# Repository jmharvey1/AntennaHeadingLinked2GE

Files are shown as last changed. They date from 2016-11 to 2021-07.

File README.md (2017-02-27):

# AntennaHeadingLinked2GE
These are the files used to link a common Antenna Rotor to Google Earth
For an overview of this project, please see YouTube Video found at:
https://youtu.be/OL32_ex3kCU

There is now a second set of files (Arduino sketch, and eagle circuit diagram) that supports
interfacing with an 8 wire CDE HAM III rotator control. 
The Python and Google Earth KLM files are the same for either interface

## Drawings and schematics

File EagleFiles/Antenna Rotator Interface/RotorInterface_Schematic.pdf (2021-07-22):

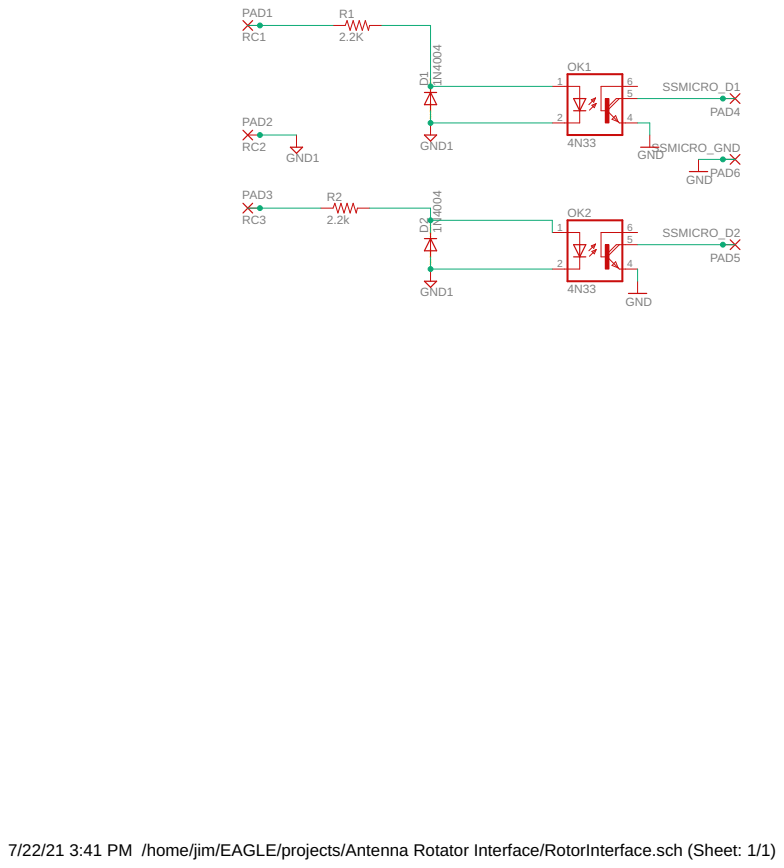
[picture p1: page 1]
GND; GND1; SSMICRO_D1; SSMICRO_D2; SSMICRO_GND; PAD1; PAD2; PAD3; PAD4; PAD5; PAD6

7/22/21 3:41 PM /home/jim/EAGLE/projects/Antenna Rotator Interface/RotorInterface.sch (Sheet: 1/1) SpiceOrder 1 SpiceOrder 2 SpiceOrder 1 SpiceOrder 2

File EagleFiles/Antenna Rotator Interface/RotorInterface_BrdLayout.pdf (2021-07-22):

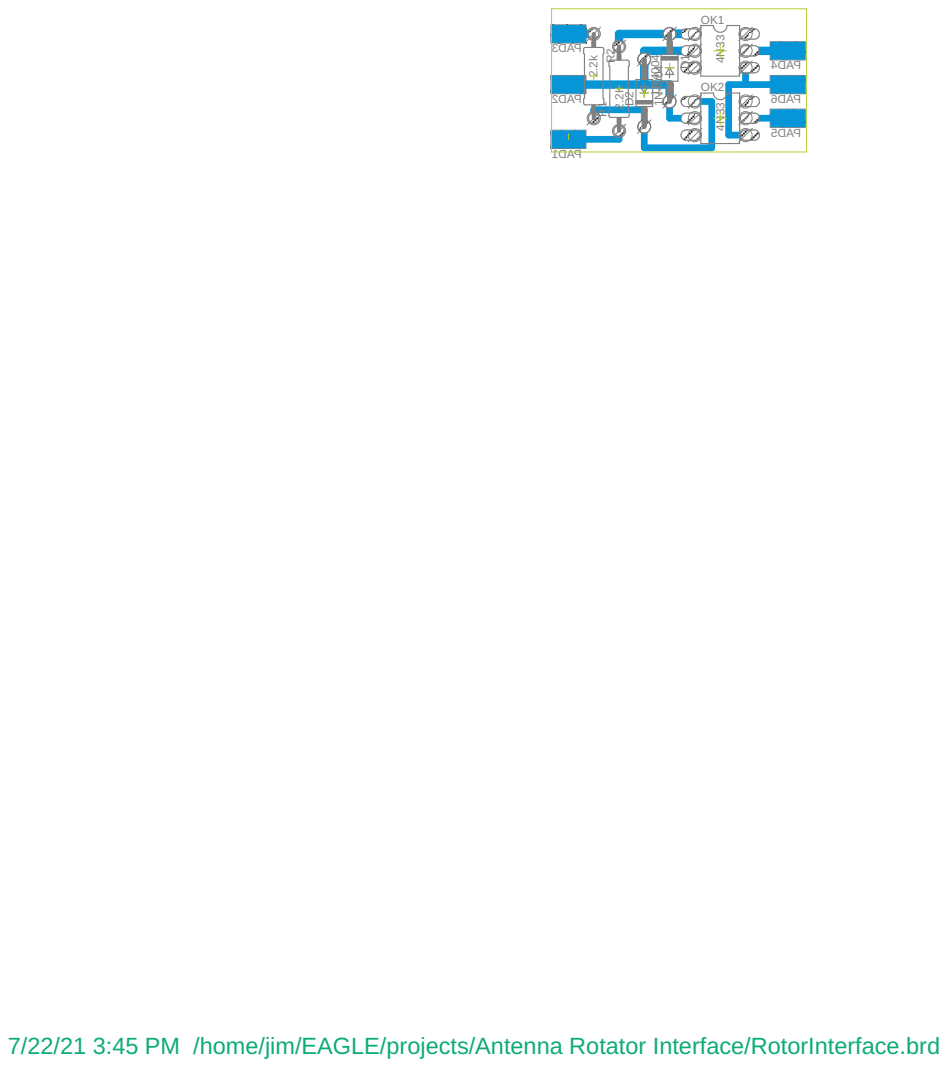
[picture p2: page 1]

7/22/21 3:45 PM /home/jim/EAGLE/projects/Antenna Rotator Interface/RotorInterface.brd

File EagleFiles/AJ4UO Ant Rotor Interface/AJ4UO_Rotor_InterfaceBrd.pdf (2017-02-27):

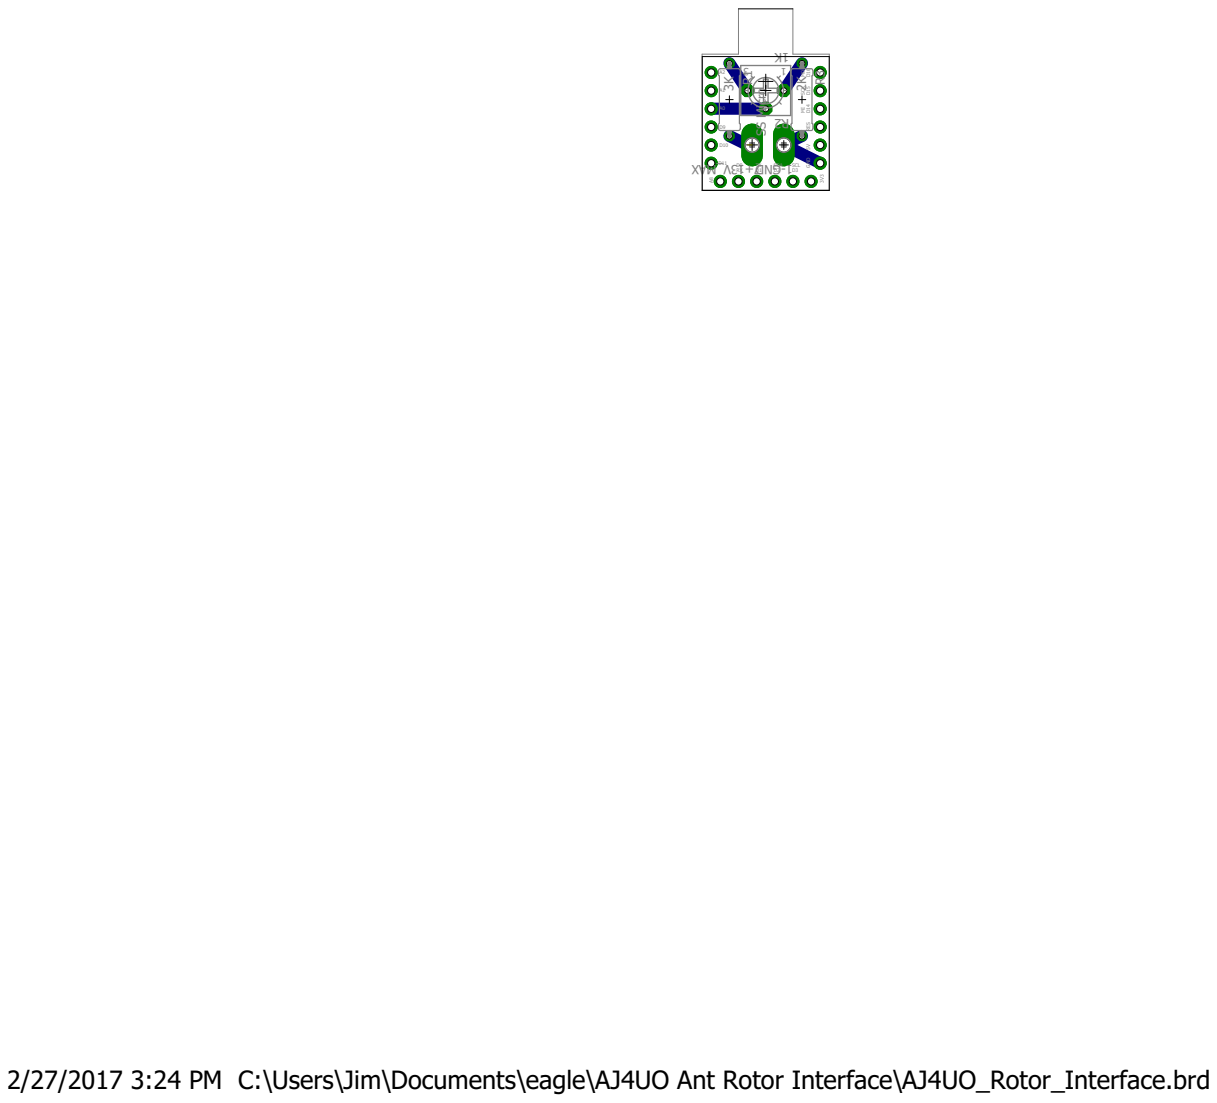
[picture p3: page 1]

2/27/2017 3:24 PM C:\Users\Jim\Documents\eagle\AJ4UO Ant Rotor Interface\AJ4UO_Rotor_Interface.brd

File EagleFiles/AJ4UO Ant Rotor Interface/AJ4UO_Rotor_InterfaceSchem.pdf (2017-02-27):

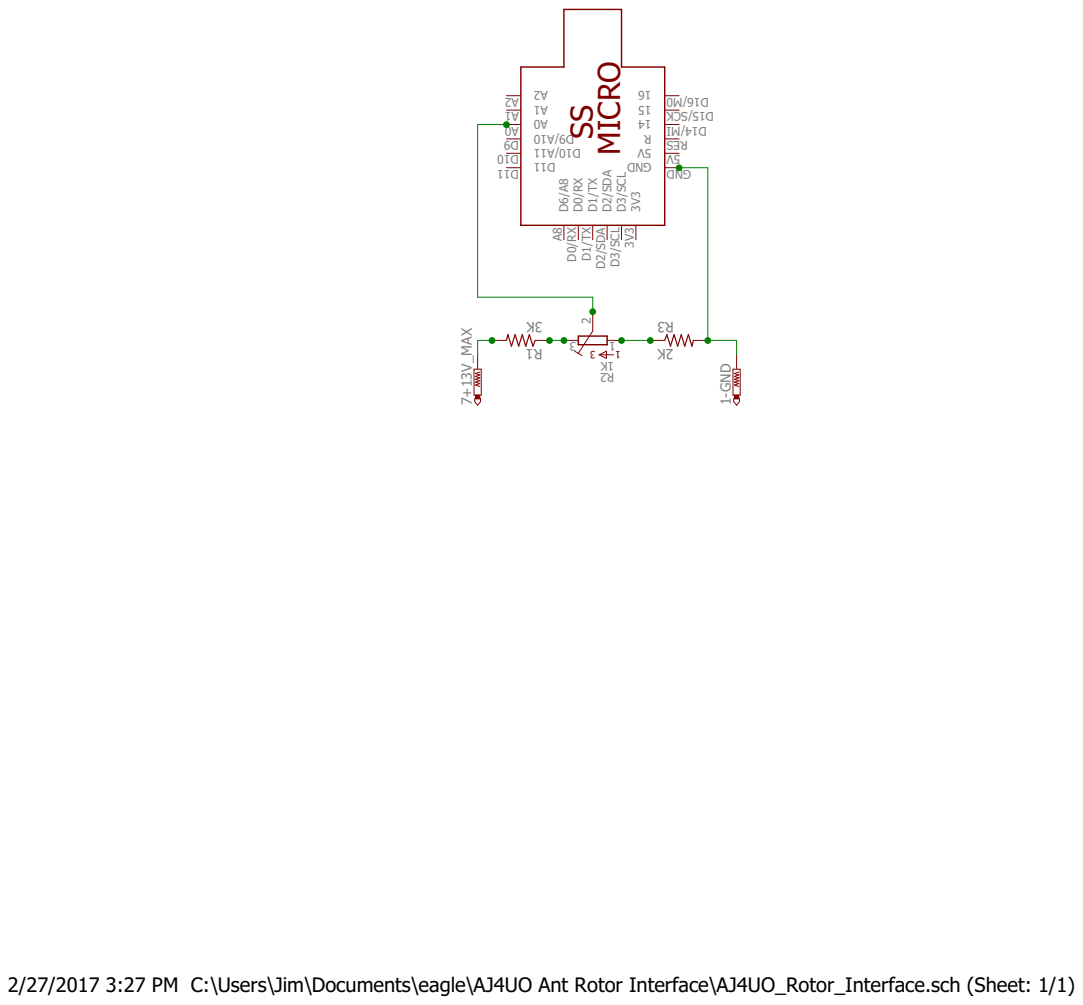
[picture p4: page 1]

D1/TX D1/TX D0/RX D0/RX D2/SDA D2/SDA D3/SCL D3/SCL

2/27/2017 3:27 PM C:\Users\Jim\Documents\eagle\AJ4UO Ant Rotor Interface\AJ4UO_Rotor_Interface.sch (Sheet: 1/1)

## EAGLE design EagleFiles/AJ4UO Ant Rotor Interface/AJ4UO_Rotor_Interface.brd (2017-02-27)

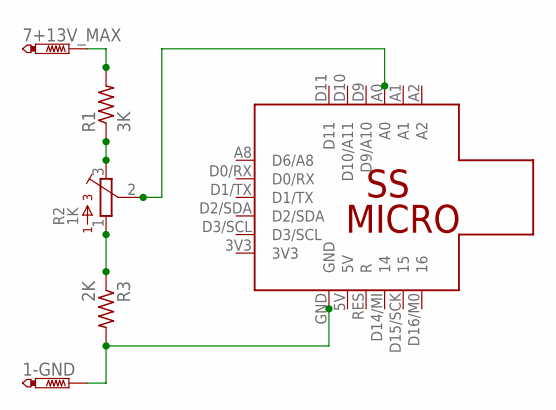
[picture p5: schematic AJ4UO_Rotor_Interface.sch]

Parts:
1-GND: 1 - GND; P1-20Y
7+13V_MAX: PTR1PAD1-20Y; P1-20Y
R1: 3K; 0309/10
R2: 1K; 3362P
R3: 2K; 0309/10
U$1: SS_MICRO

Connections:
unnamed: 1-GND.TP, R3.2, U$1.GND
unnamed: R2.1, R3.1
unnamed: R1.1, R2.3
unnamed: 7+13V_MAX.TP, R1.2
unnamed: R2.2, U$1.A0

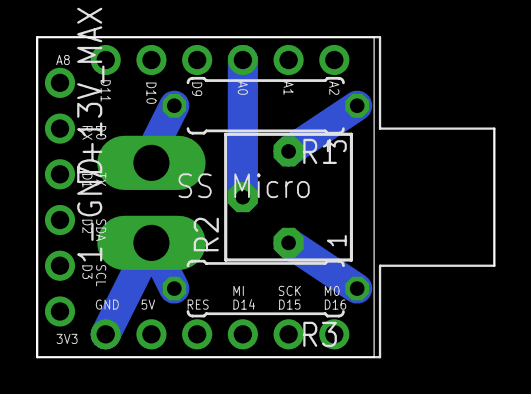
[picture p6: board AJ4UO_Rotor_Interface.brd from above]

Board: 2 copper layers, 18.7 x 17.8 mm, 6 parts (0 on the bottom side), 5 nets.

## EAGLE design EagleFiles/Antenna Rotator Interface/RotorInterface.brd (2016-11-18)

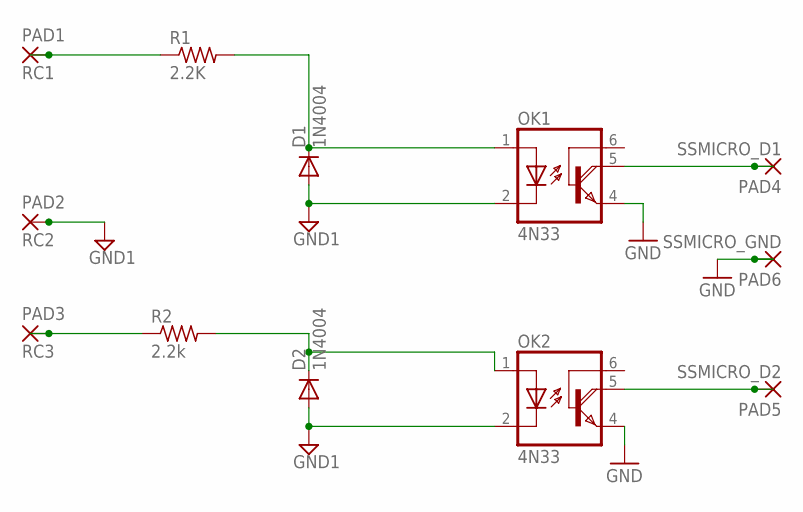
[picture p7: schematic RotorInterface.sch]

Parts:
D1, D2: 1N4004; DO41-10
OK1, OK2: 4N33; DIL06
PAD1: RC1; SMD2,54-5,08
PAD2: RC2; SMD2,54-5,08
PAD3: RC3; SMD2,54-5,08
PAD4: SSMICRO_D1; SMD2,54-5,08
PAD5: SSMICRO_D2; SMD2,54-5,08
PAD6: SSMICRO_GND; SMD2,54-5,08
R1: 2.2K; 0309/12
R2: 2.2k; 0309/12

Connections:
GND: OK1.4 (E), OK2.4 (E), PAD6.1
GND1: D1.A, D2.A, OK1.2 (C), OK2.2 (C), PAD2.1
unnamed: PAD3.1, R2.1
unnamed: PAD1.1, R1.1
unnamed: D1.C, OK1.1 (A), R1.2
unnamed: OK1.5 (COL), PAD4.1
unnamed: OK2.5 (COL), PAD5.1
unnamed: D2.C, OK2.1 (A), R2.2

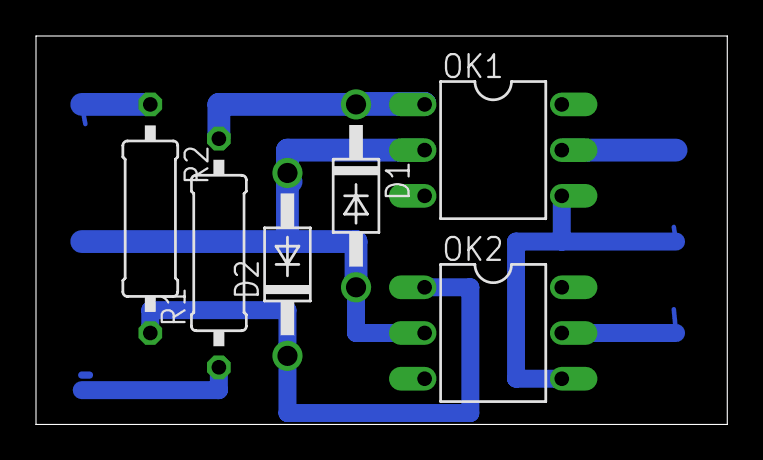
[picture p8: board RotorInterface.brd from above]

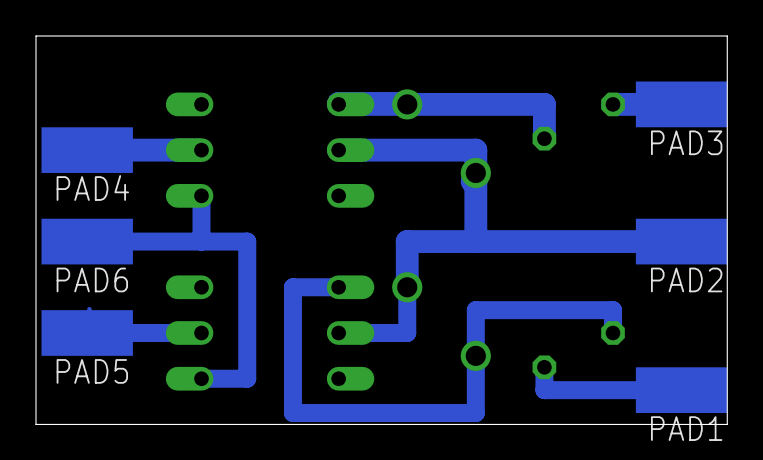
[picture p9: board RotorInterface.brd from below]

Board: 2 copper layers, 38.4 x 21.6 mm, 12 parts (6 on the bottom side), 8 nets.

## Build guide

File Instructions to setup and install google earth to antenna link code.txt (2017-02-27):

Note: The following instructions assume that "Google Earth" has been installed and is working
      on your computer. If not, download it here:
       https://earth.google.com/download-earth.html

1. To get copies of the Google Earth KML file, and the Python Script, needed for this project
   go to this Github site: 
             https://github.com/jmharvey1/AntennaHeadingLinked2GE
   Note: a recent version of the python script is also shown close to the the bottom of this file

2. To Download & Install the WAMPS server App, go to this Sourceforge location:
           https://sourceforge.net/projects/wampserver/?source=top3_dlp_t5
     or
           http://www.wampserver.com/
   
     from either of these two locations, you should be able to download the following file
          "wampserver3.0.6_x64_apache2.4.23_mysql5.7.14_php5.6.25-7.0.10.exe"      
     or the latest equivalent.
2a. Launch the execuexecutable/installer ("wampserver3.0.6_x64....  .exe") and follow the instructions

   Note: There is a Python/WAMP Server "install & setup" video found at:
               https://www.youtube.com/watch?v=bHyiXDJVjY8
   It shows the general process for installing the WAMP server and Python Applications.

3. Once installed, Start the WAMP server process (by clicking on the Desktop App ICON)
   
3a. As shown at 2:13 in the video mentioned above,
    What your are doing is modifing, the default "httpd.conf" file,
    to support Python file calls.
    To access it ("httpd.conf"), after launching the WAMP server process,
    left click the WAMP icon, in the lower tray.
    HighLight the "Apache" folder,
    And then select "httpd.conf", in the pick list that appears.

3b. Once you open the file, use notepad's "edit>find" menu option, 
    to locate the line that reads as follows:
       "# The Options directive is both complicated and important."
3c. Once located, modify the file so that it reads as shown in step 3d.

3d. When you're done, the httpd.conf file will have been modified to read as follows: 
.
.
.   
    # The Options directive is both complicated and important.  Please see
    # http://httpd.apache.org/docs/2.4/mod/core.html#options
    # for more information.
    #
    #Options +Indexes +FollowSymLinks +Multiviews
    AddHandler cgi-script .cgi .py
    Options Indexes FollowSymLinks ExecCGI
.
.
.

3e. When you are satified that your copy of "httpd.conf" matches step 3d. save and close the file.

4. Be sure that you also downloaded and installed PYTHON,
   which can be found at:
         https://www.python.org/downloads/

5. Before you can run the Python Code used in this project, You will need to add the serial
   library for python. It can be found at:
               https://github.com/pyserial/pyserial

5a. To integrate the serial library into python, 
       unzip the downloaded file "pyserial-master.zip" to known location.

5a1. Next, your Windows10 system path variable needs to be modified to include the path to Python.
     One way to find the path is, go to your start menu and and scroll down to the python folder (group)
     expand this group &
     highlight "Idle (Python3.x..)" entry.
     Right Click and use the "more > Open File location" option.
     When that folder opens, hightlight & right-click the "IDLE (Python 3.5 64-bit)" shortcut
     open the shortcut's properties window and record the "start in" location
      (on my computer, it is: "C:\Program Files\Python35\")

5a2. In the Windows 10 "Task Bar", search for "Edit the System environment Variables".    
     open the "control panel" match.
     under the "advanced" tab of the "system porperties" window, click the "environment variables" button.
     In the "System variables" section of the "enveironment variables" window, highlight the "path" entry,
     and then click the "edit" button.
     Create a "new" line entry that matches the path to python, that you recorded in step 5a1.
     (In my case, the new line entry reads: C:\Program Files\Python35 ) 

5a3. To test that the above steps worked okay, 
     start a new Command Prompt (DOS Prompt) 
     and enter the command “python”. 
     You should see something like this:
 	Python 3.5.2 (v3.5.2:4def2.....)[MSC v.1900 64 bit (AMD64)] on win32
	type "help", "copyright", "credits" or "license" for more information.
	>>>>
5a4. To close Python, and to return back to the command prompt, type: exit() , and hit the "enter" key.

5a5. Now, while still in the Dos command prompt window, navigate to your extracted "pyserial-master" folder.

5a6. Once there, enter the command: "python setup.py install" (do not include the quotes)
     this should generate quite a long respone, that ends with statements looking something like 
     the following:
          Installed c:\program files\python35\lib\site-packages\pyserial-3.2.1-py3.5.egg
          Processing dependencies for pyserial==3.2.1
          Finished procesing dependenciesnfor pyserial==3.2.1

6. Move/Copy the Python file ("viewCenteredPlacemark.py", downloaded from the github site, Step1) to: 
     C:\wamp64\www

   Note: For reference, this python script/file reads as follows:

#!C:\Program Files\Python35\python

import cgi
import math
from datetime import datetime
import serial
import time

# the following 3 lines will need to be modified to match your setup/ & location
center_lng = -85.198159 #Antenna's GPS Longtitude
center_lat = 35.123637 #Antenna's GPS Latitude
ser = serial.Serial('COM10', 9600, timeout=0)

url = cgi.FieldStorage()
heading = 0.0   
try:
  ser.write(b'OK2Snd\n')
  time.sleep(0.05)
  val1 = ser.readline()
  if val1:
      try:
        heading = float(val1)
      except ValueError:
        message = "Either val1 ({!r}) is not a valid number".format(val1)
        ##print("Error!", message)
        tkMessageBox.showerror("Invalid Inputs", message)  
      ##print( heading)
      ##time.sleep(0.5)
except ser.SerialTimeoutException:
  tkMessageBox.showerror("Data could not be read")

##bbox = url['BBOX'].value
##bbox = bbox.split(',')
##west = float(bbox[0])
##south = float(bbox[1])
##east = float(bbox[2])
##north = float(bbox[3])
##
##center_lng = ((east - west) / 2) + west
##center_lat = ((north - south) / 2) + south

R = 6378.1 #Radius of the Earth
brng = math.radians(heading) #heading is 90 degrees converted to radians.
d = 40              #Distance in km
d = math.pi*R*0.99  #Distance in km

lat1 = math.radians(center_lat) #Current lat point converted to radians
lon1 = math.radians(center_lng) #Current long point converted to radians

lat2 = math.asin( math.sin(lat1)*math.cos(d/R) +
     math.cos(lat1)*math.sin(d/R)*math.cos(brng))

lon2 = lon1 + math.atan2(math.sin(brng)*math.sin(d/R)*math.cos(lat1),
             math.cos(d/R)-math.sin(lat1)*math.sin(lat2))

lat2 = math.degrees(lat2)
lon2 = math.degrees(lon2)

kml = ( 
   '<?xml version="1.0" encoding="UTF-8"?>\n'
   '<kml xmlns="http://www.opengis.net/kml/2.2">\n'
   '<Document>\n'
   '<Style id="Mylinestyle">\n'
   '<LineStyle>\n'
   '<color>7f0000ff</color>\n'
   '<width>4</width>\n'
   '</LineStyle>\n'
   '</Style>\n'
   '<Placemark>\n'
   '<name>Heading: {4:.0f}</name>\n'
   '<styleUrl>#Mylinestyle</styleUrl>\n'
   '<LineString>\n'
   '<extrude>1</extrude>\n'
   '<tessellate>1</tessellate>\n'
   '<coordinates>\n'
   '{0:.14f},{1:.14f},0 {2:.14f},{3:.14f},0\n'
   '</coordinates>\n'
   '</LineString>\n'
   '</Placemark>\n'
   '</Document>\n'
   '</kml>'
   ) .format(center_lng, center_lat, lon2, lat2, heading)

print('Content-Type: application/vnd.google-earth.kml+xml\n')
print(kml)

##### End of Python Script #################

7. Before running/using the above file, modify these 3 lines: 
	center_lng = -85.198159 #Your Antenna's GPS Longtitude
	center_lat = 35.123637 #Your Antenna's GPS Latitude
	ser = serial.Serial('COM10', 9600, timeout=0)
   to match your setup.

7a. Also the first line, in the viewCenteredPlacemark.py file, which currently reads as follows:
      #!C:\Program Files\Python35\python
    It needs to be changed match your “path” to python
    So if your path to python is different, adjust this line to read:
    #!........yourpath.......\python

8. And finally, Note:
   The "d=..." line in the above python file can be modified to set the length of the
   "red heading" line as seen on Google Earth. Change this line to meet your needs.

9. Now place the kml file "networklinkTest02.kml" in any convient location. For example:
           "My Documents/GoogleEarthKMLfile"

10. That's it. If all went well. Plug in your SS Micro interface. 
    Start WAMPS. 
    Wait for the ICON to trun green. (If it doesn't turn "green", see step 11 for possible fix)
    And then, start Google Earth

10a. Using the "file > Open" menu option (in Google Earth), navigate to "networklinkTest02.kml",
     and select and open it via this dialog box

10b. The first time you run Google Earth with the new KML file (and shut Google Earth down), 
     it will ask you to "Save the Temporary Places" Entry. 
     Click "yes". 
     That should coplete the install process. 
-----------------------------------------------------------------------------------------------------

11   Fix for Wamp services not starting (Icon won't turn green)
11a. Search for "Turn Windows features on or off" on the taskbar.
11b. Under "Internet Information Services" deselect "World Wide Web Services" .
11c. Reboot and WAMP should now go "green".

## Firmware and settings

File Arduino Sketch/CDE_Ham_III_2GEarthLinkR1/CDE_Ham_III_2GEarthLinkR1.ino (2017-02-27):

/*  This Sketch was written to support interfacing with
 *  CDE HAM III Antenna rotator systems.
 *  As written it assumes that the control box has no modifications
 *  and is wired per the Owner's manual wiring diagram.
 *  And as such, expects terminal 1 on the control box to be Chasis ground,
 *  and +13VDC will be found between terminals 3 and 7. 
 *  And finally, when the Antenna is rotated to the zero degree heading, 
 *  there will be +13VDC measured from chasis ground to terminal 7.
 *  and then when the antenna is rotated to the 360 degree position, 
 *  the voltage between chasis ground (terminal 1) and terminal 7 will be 0VDC.
 *  It futher assumes that the voltage vs Antenna heading is linear.
 *  
 *  The 1K interface trim pot should be adjusted at the zero degree heading,
 *  and should be adjusted such that the red led on the micro just turns OFF
 */

String Dir = "";
float CurHeading = 0.0;
float HeadingInc = 0.0;
String inputString = "";         // a string to hold incoming data
boolean stringComplete = false;  // whether the string is complete
int bearing = 0;
int MinSensVal = 38;  // set to value greater than zero if auto zero calibration is desired
int MaxSensVal = 1000;  // set to value greater than zero if auto zero calibration is desired
int LastSensVal = 0;
int sensorPin = A0;    // select the input pin for the potentiometer
int sensorValue = 0;  // variable to store the value coming from the sensor
//int ledPin = 6;      // select the pin for the LED



void setup(){
  // Open serial connection.
  Serial.begin(9600);
  // reserve 200 bytes for the inputString:
  inputString.reserve(200);
  // declare the ledPin as an OUTPUT:
  //pinMode(ledPin, OUTPUT);
  HeadingInc = 360.0/(MaxSensVal - MinSensVal);
  Dir.reserve(5); // reserve 5 bytes for the Dir:
}
 
void loop(){
 if ( stringComplete){  
   //Serial.print(inputString);
   //Serial.println(": Hello world");
   bearing = (int)CurHeading;
   //Adjust for "north" being at mid scale
   if (bearing >= 180) bearing = 540 - bearing;
   else bearing = 180 - bearing;
   Serial.println(bearing);
   inputString = "";
   stringComplete = false;
  }
  // read the value from the sensor:
  sensorValue = analogRead(sensorPin);
  if (sensorValue > 1000)   RXLED1;      //Turn RXLED pin on //digitalWrite(ledPin, HIGH); // turn the ledPin on
  else  RXLED0;      //Turn RXLED pin off //digitalWrite(ledPin, LOW); // turn the ledPin OFF
  // now limit moment to moment change to a change of 10 counts
  if (sensorValue >LastSensVal+10) sensorValue = LastSensVal+10;
  if (sensorValue <LastSensVal-10) sensorValue = LastSensVal-10;
  LastSensVal = sensorValue; 
  //auto zero calibration
//  if (sensorValue < MinSensVal){
//    MinSensVal = sensorValue;
//    HeadingInc = 360.0/(MaxSensVal - MinSensVal);
//  }
  if (sensorValue > MaxSensVal & sensorValue<= 1000){
    MaxSensVal = sensorValue;
    HeadingInc = 360.0/(MaxSensVal - MinSensVal);
  }
  //treat this sample to be part of a running 10 sample average
  CurHeading = ((9*CurHeading)+(360.0 - HeadingInc*(sensorValue-MinSensVal)))/10 ;
  delay(50);
  MyserialEvent();
}

/*
  SerialEvent occurs whenever a new data comes in the
 hardware serial RX.  This routine is run between each
 time loop() runs, so using delay inside loop can delay
 response.  Multiple bytes of data may be available.
 */
void MyserialEvent() {
  while (Serial.available()) {
    // get the new byte:
    char inChar = (char)Serial.read();
    // if the incoming character is a newline, set a flag
    // so the main loop can do something about it:
    if (inChar == '\n') {
      stringComplete = true;
    }
    else inputString += inChar;  // add it to the inputString:
  }
}

      

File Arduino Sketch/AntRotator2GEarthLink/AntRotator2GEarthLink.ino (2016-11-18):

#define FullCircleCnt 3780 //3780
String Dir = "";
bool AllOff = false;
bool Running = false;
float CurHeading = 0.0;
float HeadingInc = 0.0;
float RunOn = 2.0; // Number Degrees Antenna continues to rotate after power is cur
unsigned long Start; 
unsigned long period;
int cnt =0;
int cntU =0;
int cntD =0;
String inputString = "";         // a string to hold incoming data
boolean stringComplete = false;  // whether the string is complete
int bearing = 0;

void setup(){
// Open serial connection.
Serial.begin(9600);
 // reserve 200 bytes for the inputString:
  inputString.reserve(200);
   pinMode(14, INPUT_PULLUP);
  pinMode(15, INPUT_PULLUP);
  HeadingInc = 360.0/FullCircleCnt;
  Dir.reserve(5); // reserve 5 bytes for the Dir:
}
 
void loop(){
 if ( stringComplete){  
  //Serial.print(inputString);
  //Serial.println(": Hello world");
  bearing = (int)CurHeading;
  Serial.println(bearing);
  inputString = "";
  stringComplete = false;
  //bearing +=2;
  //if (bearing == 360) bearing = 0;
 }
 //delay(10); // ms
 int Pin14Val = digitalRead(14);
  int Pin15Val = digitalRead(15);
  if (Pin14Val & Pin15Val){
    if (!AllOff) Start = micros();
    AllOff = true;
    period = micros()-Start;
    if (period >16666 & Running){// been stopped for more than a cycle
      if(cntU > cntD) CurHeading +=  RunOn;
      if(cntU < cntD) CurHeading -=  RunOn;
      ChkLimits();
      //Serial.println(cnt);
      //Serial.print("Heading: ");
      //Serial.println(CurHeading);
      cnt =0;
      cntU =0;
      cntD =0;
      Running = false;
    }
  }
  if (AllOff & (!Pin15Val || !Pin14Val)){
    if (!Pin14Val & Pin15Val) Dir ="^";
    if (!Pin15Val & Pin14Val) Dir ="_";
    if (!Pin15Val & !Pin14Val){
      //Serial.print(Dir);
      AllOff = false;
      cnt ++;
      if(Dir == "^") cntU ++;
      if(Dir == "_") cntD ++; 
      if (cntU > cntD) CurHeading +=  HeadingInc;
      if (cntU < cntD) CurHeading -=  HeadingInc;
      ChkLimits();
      Dir ="+";
      Running = true;
    }
  }
 MyserialEvent();
}

/*
  SerialEvent occurs whenever a new data comes in the
 hardware serial RX.  This routine is run between each
 time loop() runs, so using delay inside loop can delay
 response.  Multiple bytes of data may be available.
 */
void MyserialEvent() {
  while (Serial.available()) {
    // get the new byte:
    char inChar = (char)Serial.read();
    // if the incoming character is a newline, set a flag
    // so the main loop can do something about it:
    if (inChar == '\n') {
      stringComplete = true;
    }
    else inputString += inChar;  // add it to the inputString:
  }
}

void ChkLimits(){
      if(CurHeading <0.0) CurHeading=0.0;
      if(CurHeading >=360.0) CurHeading=359.9;
}      

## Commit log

2016-11-18 Initial project files setup
    Install base set of project files
    [RotorInterface.brd, RotorInterface.sch]
2017-02-27 Added files to also support interfacing with a CDE HAM III rotator control
    [AJ4UO_Rotor_Interface.brd, AJ4UO_Rotor_Interface.sch]
2021-07-22 Added .pdf files for original interface board
    Added .pdf files for Eagle interface board (shematic & Layout)
